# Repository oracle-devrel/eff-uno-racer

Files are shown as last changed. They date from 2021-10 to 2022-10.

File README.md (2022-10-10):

# Oracle Cloud Controlled Open Wheel Race Car

 

## Introduction
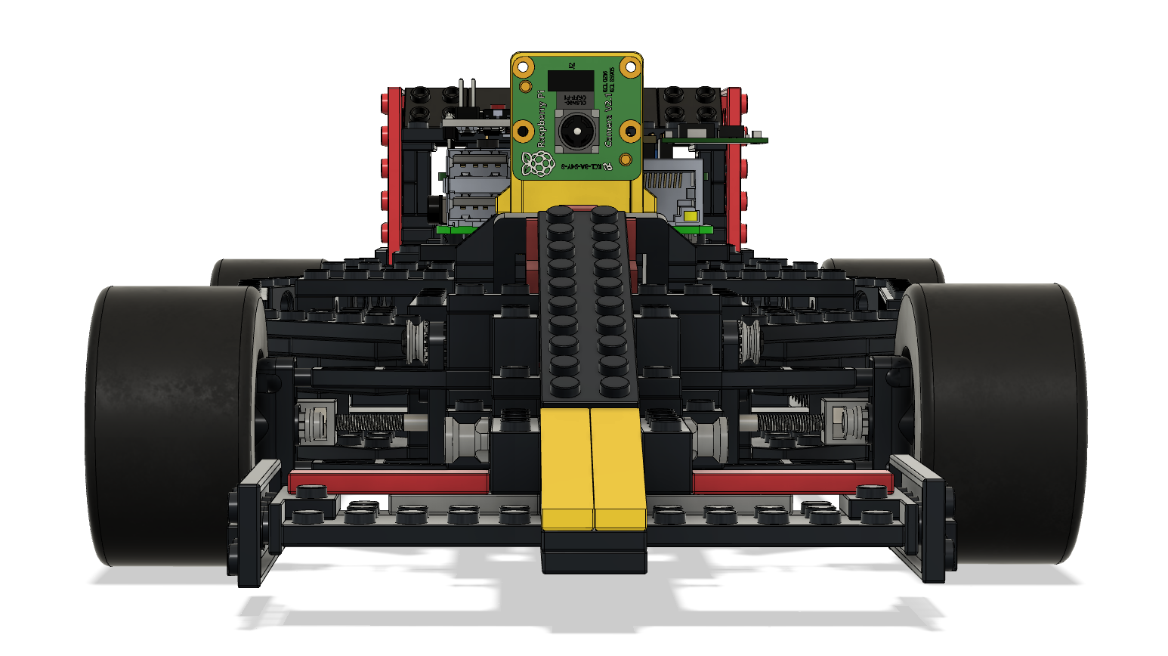
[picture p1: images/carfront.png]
CAD Model of Eff-Uno Racer


Welcome to the Eff-Uno Racer, or FUR1. This is a cloud controlled brick open wheel race car that anyone can build and this is the repository for everything related to this build.

## Getting Started
MISSING

### Prerequisites
MISSING

## Notes/Issues
MISSING

## URLs
* Nothing at this time

## Contributing
This project is open source.  Please submit your contributions by forking this repository and submitting a pull request!  Oracle appreciates any contributions that are made by the open source community.

## License
Copyright (c) 2021 Oracle and/or its affiliates.

Licensed under the Universal Permissive License (UPL), Version 1.0.

See [LICENSE](LICENSE) for more details.

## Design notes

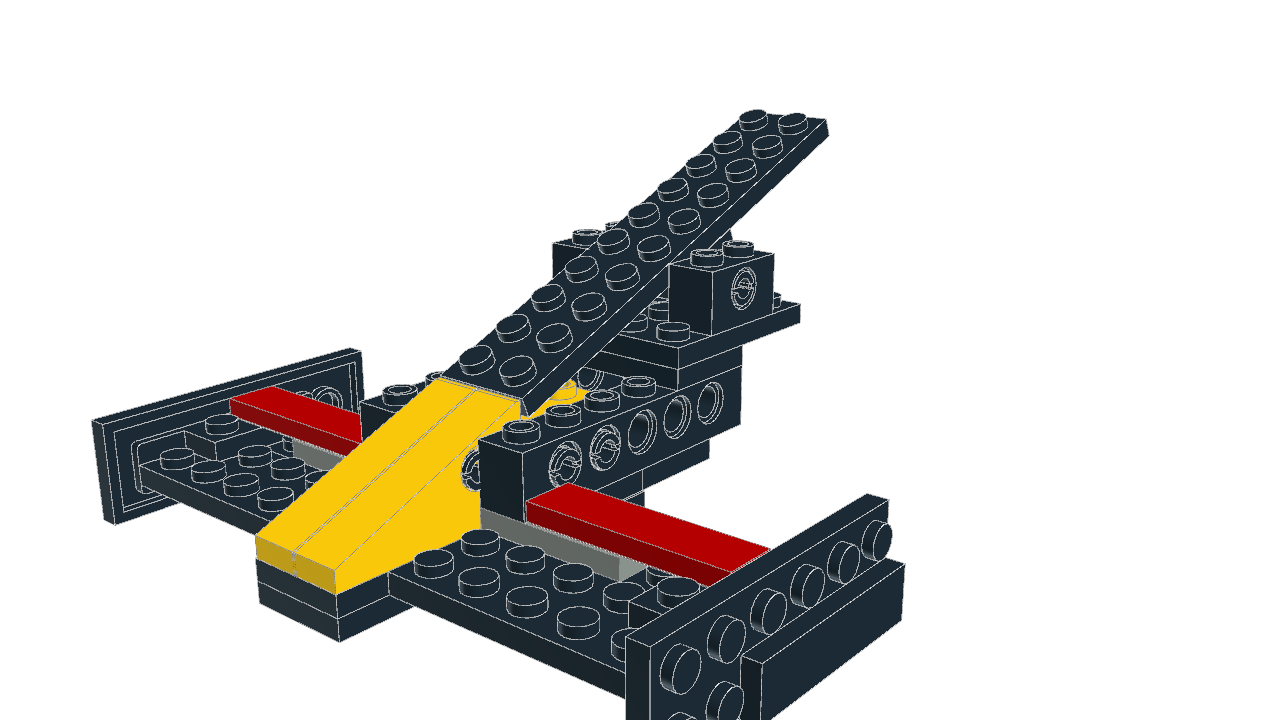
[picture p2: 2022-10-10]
models/FUR1.png

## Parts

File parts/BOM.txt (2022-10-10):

----------------------------------------------------------------------
Tools
Hex wrench 2mm and Mmm
https://amzn.to/3je7wY7

Installation Tip for 4-40/M2.5 x 0.45 Thread Size Heat-Set Inserts for Plastics
https://www.mcmaster.com/92160A115/

----------------------------------------------------------------------
Motor

(1) ESC + Brushless DC Motor
https://amzn.to/3jecPXt

(1) Gear set screw M3 
Stainless Steel Flat-Tip Set Screw18-8 M3 x 0.5 mm Thread 3 mm Long
https://www.mcmaster.com/92605A097
92605A097_Stainless Steel Flat-Tip Set Screw.STEP

(4) brushless DC motor bolts
18-8 Stainless Steel Hex Drive Flat Head ScrewM3 x 0.5 mm Thread 8 mm Long
https://www.mcmaster.com/92125A128/
92125A128_18-8 Stainless Steel Hex Drive Flat Head Screw.STEP

----------------------------------------------------------------------
Servo

(1) Servo Motor
https://amzn.to/2WjmpiD

(4) servo motor bolts
18-8 Stainless Steel Hex Drive Flat Head Screw M3 x 0.5 mm Thread, 10 mm Long
https://www.mcmaster.com/92125A130/
92125A130_18-8 Stainless Steel Hex Drive Flat Head Screw.STEP

(4) Servo motor nuts
18-8 Stainless Steel Hex NutM3 x 0.5 mm Thread
https://www.mcmaster.com/91828A211/
91828A211_18-8 Stainless Steel Hex Nut.STEP

----------------------------------------------------------------------
Pi

(1) Pi 4
Raspberry Pi 4 Model B (8 GB)
https://www.sparkfun.com/products/16811

(4) Bolts to hold Pi
Button Head Hex Drive ScrewPassivated 18-8 Stainless Steel M2.5 x 0.45 mm Thread 16mm Long
https://www.mcmaster.com/91292A018/

(4) Threaded inserts to hold Pi bolt
Tapered Heat-Set Inserts for PlasticBrass M2.5 x 0.45 mm Thread Size 3.4 mm Installed Length
https://www.mcmaster.com/94180A321/

----------------------------------------------------------------------
Pi Camera

(1) Pi 4 Camera
Raspberry Pi Camera Module V2
https://www.sparkfun.com/products/14028

(4) Pi camera bolts
18-8 Stainless Steel Socket Head Screw M2 x 0.4 mm Thread, 8 mm Long
https://www.mcmaster.com/91292A832/
91292A832_18-8 Stainless Steel Socket Head Screw.STEP

(4) Pi camera nuts
18-8 Stainless Steel Hex Nut M2 x 0.4 mm Thread
https://www.mcmaster.com/91828A111/
91828A111_18-8 Stainless Steel Hex Nut.STEP

(4) Pi camera washers
18-8 Stainless Steel Washer
for M2 Screw Size, 2.2 mm ID, 5 mm OD
https://www.mcmaster.com/93475A195/
93475A195_18-8 Stainless Steel Washer.STEP

----------------------------------------------------------------------
Steering

(2) Long bolt for the steering
18-8 Stainless Steel Socket Head Screw M3 x 0.5 mm Thread, 40 mm Long
https://www.mcmaster.com/91292A024/
91292A024_18-8 Stainless Steel Socket Head Screw.STEP

(2) sterring rod nuts
18-8 Stainless Steel Hex NutM3 x 0.5 mm Thread
https://www.mcmaster.com/91828A211/
91828A211_18-8 Stainless Steel Hex Nut.STEP

----------------------------------------------------------------------
Alternatives

Set screws
https://amzn.to/3gqRpV6

M3 & M3 bolts + nuts
https://amzn.to/3gO2LTx

Alternative battery charger

----------------------------------------------------------------------
Electronics

(1) 

(1) Arduino Micro
https://store.arduino.cc/products/arduino-micro

(1) Sparkfun ICM-20948 accelerometer
https://www.sparkfun.com/products/17241

(1) Pololu D24V50F5 voltage regulator
https://www.pololu.com/product/2851

(5) 10K resistor
(1) 220 resistor
https://www.sparkfun.com/products/10969

(2) 10uF 16V capacitor
https://www.amazon.com/Electrolytic-Capacitors-Capacitor-Conditioning-Refrigerator/dp/B08L5ZL87P

(2) 2N7000
https://www.amazon.com/CHANZON-100pcs-2N7000-Transistor-Channel/dp/B083TF4K6L

(1) PN2222
https://www.sparkfun.com/products/13689
https://www.amazon.com/Adafruit-NPN-Bipolar-Transistors-PN2222/dp/B00XW2OK7M

(1) FQP30N06L
https://www.amazon.com/BOJACK-RFP30N06LE-MOSFET-N-Channel-Transistor/dp/B07WR86ZGS

(1) 5 pin 0.1" (2.54mm) pitch header single row male for voltage regulator
5 pin female header 1.0 pitch
https://www.sparkfun.com/products/18218

(1) 6 pin 0.1" (2.54mm) pitch header single row male for accelerometer
6 pin female header 1.0 pitch
https://www.sparkfun.com/products/18219

(2) 17 or 18 pin 0.1" (2.54mm) pitch header single row male for Arduino
18 pin female header 1.0 pitch
Female Header
https://www.mouser.com/ProductDetail/3M-Electronic-Solutions-Division/929870-01-18-RA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
https://www.amazon.com/gp/product/B07CGGSDWF/ref=ppx_yo_dt_b_asin_title_o00_s00?ie=UTF8&psc=1
https://www.sparkfun.com/products/115

(1) 2x20 female 0.1" (2.54mm) pitch headers for the pi
Pi Header
https://www.sparkfun.com/products/14017
https://www.amazon.com/gp/product/B00R1LLM1M/ref=ppx_yo_dt_b_asin_title_o00_s00?ie=UTF8&psc=1

Male Header
https://www.sparkfun.com/products/116

Wire
https://www.amazon.com/BNTECHGO-Silicone-Flexible-Strands-Stranded/dp/B01AO7586O

----------------------------------------------------------------------
Battery

(2) Battery
https://amzn.to/3kslEwi

Detail modifications to the battery

(1) Battery charger
https://amzn.to/3zrWhAE
https://hobbyking.com/en_us/turnigy-reaktor-touch-300-ac-dc-20a-1-6s-300w-touch-screen-balance-charger-us-plug.html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

----------------------------------------------------------------------

----------------------------------------------------------------------

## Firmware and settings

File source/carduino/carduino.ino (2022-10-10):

#include <Wire.h>
#include <Servo.h>

// Board: Arduino Micro
// Programmer: AVR ISP

#define CASE_MOTOR 1
#define CASE_SERVO1 2
#define CASE_SET_SERVO1_MIN 20
#define CASE_SET_SERVO1_MAX 21
#define CASE_SERVO2 3
#define CASE_SET_SERVO2_MIN 30
#define CASE_SET_SERVO2_MAX 31
#define CASE_LED 4

// 2 (SDA)
// 3 (SCL)
int escPin = 11;
int servo1Pin = 9;
int servo2Pin = 10;
//int tempProbe1Pin = 23;
//int tempProbe2Pin = 24;
int ledPin = 13;
//int rocketPin = 31;

//byte PWM_PIN = 6;

int i2cAddress = 0x8;

Servo esc;
Servo servo1;
Servo servo2;

int status = 0;

int motorMin = 1000;
int motorMax = 2000;
int servo1Min = 0;
int servo1Max = 180;
int servo2Min = 0;
int servo2Max = 180;

#define motorStop 1500
#define servo1Center 79

#define ERROR_READING 1
#define INVALID_RANGE 2

void setup() {
  Serial.begin(115200);

  Wire.begin(i2cAddress);
  Wire.onReceive(receiveEvent);
  Wire.onRequest(requestEvent);

  esc.attach(escPin, motorMin, motorMax); // pin, min pulse width, max pulse width in microseconds
  delay(1000);
  esc.write(motorStop);                   // initialize the ESC
  delay(3000);

  servo1.attach(servo1Pin, servo1Min, servo1Max); // pin, min pulse width, max pulse width in microseconds
  delay(1000);
  servo1.write(servo1Center);
  servo1Min = 50;
  servo1Max = 90;
  
  servo2.attach(servo2Pin, servo2Min, servo2Max); // pin, min pulse width, max pulse width in microseconds

  pinMode(ledPin, OUTPUT);
  digitalWrite(ledPin, LOW);

  //pinMode(A4, INPUT_PULLUP);

//  pinMode(PWM_PIN, INPUT);

  Serial.println("starting");
}

int motorspeed = 1500;
int currentspeed = 1500;
//int pwm_value;

void loop() {
  if (currentspeed != motorspeed) {
    currentspeed = step(motorspeed, currentspeed);
    esc.write(currentspeed);
    Serial.println(currentspeed);
    delay(10);
  }

  //Serial.println(analogRead(A4));
  //pwm_value = pulseIn(PWM_PIN, HIGH);
  //Serial.println(pwm_value);
}

boolean range(int min, int max, int value) {
  return (min <= value) && (value <= max);
}

// linear interpolation
int interpolate(int value, int minIn, int maxIn, int minOut, int maxOut) {
  int temp = (value - minIn) / (maxIn - minIn);
  return minOut + (maxOut - minOut) * temp;
}

int step(int goal, int value) {
  int result = value;
  
  if (motorspeed > result) {
    result++;
  }
  else if (motorspeed < result) {
    result--;
  }

  return result;
}

void receiveEvent(int byteCount) {
  Serial.print("receiveEvent: "); 
  Serial.println(byteCount);

  if (byteCount > 1) {
    byte message = Wire.read();
 
    switch (message) {
      case CASE_MOTOR: {
        int speed = 0;   
      
        if (byteCount == 3) {
          byte high = Wire.read();
          byte low = Wire.read();
          Serial.println(high);
          Serial.println(low);
          speed = 0;
          speed = (high << 4) | low;
        }
        else {
          speed = Wire.read();
        }
        
        Serial.print("esc: ");
        Serial.println(speed);

        if (range(motorMin, motorMax, speed)) {
          //esc.write(speed); TODO Remove. Moved to loop for linear interpoloation
          motorspeed = speed;
          Serial.println("success");
        }
        else {
          status = INVALID_RANGE;
        }
        
        break;
      }

      case CASE_SERVO1: {
        byte degrees = Wire.read();
        Serial.print("servo: ");
        Serial.println(degrees);

        //50 max left
        //70 center
        //90 max right
        //degrees = interpolate(degrees, 50, 90, 0, 180);
          
        if (range(servo1Min, servo1Max, degrees)) {
          servo1.write(degrees);
          Serial.println("success");
        }
        else {
          status = INVALID_RANGE;
        }
        
        break;
      }

      case CASE_SET_SERVO1_MIN: {
        byte min = Wire.read();
        Serial.print("set servo1 min: ");
        Serial.println(min);
        servo1Min = min;
        Serial.println("success");
        break;                
      }

      case CASE_SET_SERVO1_MAX: {
        byte max = Wire.read();
        Serial.print("set servo1 max: ");
        Serial.println(max);
        servo1Max = max;
        Serial.println("success");
        break;  
      }


      case CASE_SERVO2: {
        byte degrees = Wire.read();
        Serial.print("servo: ");
        Serial.println(degrees);

        //50 max left
        //70 center
        //90 max right
        //degrees = interpolate(degrees, 50, 90, 0, 180);
          
        if (range(servo2Min, servo2Max, degrees)) {
          servo2.write(degrees);
          Serial.println("success");
        }
        else {
          status = INVALID_RANGE;
        }
        
        break;
      }

      case CASE_SET_SERVO2_MIN: {
        byte min = Wire.read();
        Serial.print("set servo1 min: ");
        Serial.println(min);
        servo2Min = min;
        Serial.println("success");
        break;                
      }

      case CASE_SET_SERVO2_MAX: {
        byte max = Wire.read();
        Serial.print("set servo1 max: ");
        Serial.println(max);
        servo2Max = max;
        Serial.println("success");
        break;  
      }

      case CASE_LED: {
        byte state = Wire.read();

        if (state == 0) {
           digitalWrite(ledPin, LOW);
           Serial.println("success led off");
        }
        else if (state == 1) {
           digitalWrite(ledPin, HIGH);
           Serial.println("success led on");
        }
        break;
      }
      
      default: {
        status = ERROR_READING;
      }
    }
  }
}

void requestEvent() {
  Serial.print("requestEvent ");
  Serial.println(status);
  Wire.write(status);
}

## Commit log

2021-06-23 Creating/updating sonar-project.properties on main
2021-12-17 CAD model
2022-01-20 Update PCB
    [PiRaceHat-B_Cu.gbr, PiRaceHat-B_Mask.gbr, PiRaceHat-B_SilkS.gbr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]
2022-03-25 Update to model and to arduino sketch
2022-03-26 ramping up of motor speeds
2022-03-29 initialize servo with correct end stops and center position.
    [carduino.ino]
